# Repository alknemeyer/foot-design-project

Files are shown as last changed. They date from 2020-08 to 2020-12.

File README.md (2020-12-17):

# Foot Design Project

_Code for the hopper being used to test foot designs_

This project was developed by [Alexander Knemeyer](https://github.com/alknemeyer) on a laptop running PopOS (_basically_ Ubuntu). I can't think of a reason why the project wouldn't work under Windows/MacOS, though the commands were all written with Linux in mind. Please don't hesitate to ask me questions!

Read the following four blog posts to get you up and running with Python workflows and embedded dev:
* Communicating with embedded systems using Python, [part 1](https://alknemeyer.github.io/embedded-comms-with-python/) and [part 2](https://alknemeyer.github.io/embedded-comms-with-python-part-2/)
* [A workflow for remote development](https://alknemeyer.github.io/remote-notebooks/)
* [Improving the jupyter notebook workflow](https://alknemeyer.github.io/jupyter-notebook-workflow/)

The last two are themed on "remote" and "jupyter notebook" development, but are useful for this project

## The robot

A rough model of the robot, describing angle conventions, lengths, etc. Made using https://editor.method.ac/ - a free online svg editor. Stick to this! And keep it up to date!

<p align="center">

</p>

### Equipment used

| Item | Name |
| --- | --- |
| Motor controller | [ODrive](https://odriverobotics.com/) |
| Motor x2 | [T-motor U-10 80rpm/V](http://store-en.tmotor.com/goods.php?id=362) |
| Motor encoder x2 | [HEDL-5640-A13](https://www.mouser.co.za/ProductDetail/Broadcom-Avago/HEDL-5640A13?qs=RuhU64sK2%252Bv3nPu5sOD%2FhQ==) |
| Force sensor | [OptoForce OMD-45-FH-2000N](http://schlu.com/pdf/Optoforce_Sensore_di_forza_3D_OMD-45-FH-2000N_1.5_EN.pdf) |
| Sensor logger | [Parts list](https://github.com/African-Robotics-Unit/sensor-logger)|

### Wiring things together

The general setup is:
| | | Connection type |
|-|-|---:|
| laptop | sensor logger | USB cable |
| laptop | ODrive | USB cable |
| ODrive | motor encoders | Premade connectors. See below |
| ODrive | motors | Three thick wires for each motor |
| ODrive "AUX" port | 10 Ohm shunt resistor | Short thick wires |
| laptop | OptoForce | USB connection |

I can't remember how to do the calculation for the required resistance/power, unfortunately!

The motor encoders have pins as follows:

| pin | type | | pin | type |
|-----|---|-|-----|---|
| 1 | NC | | 2 | +5V  |
| 3 | GND | | 4 | NC |
| 5 | not(A) | | 6 | A |
| 7 | not(B) | | 8 | B |
| 9 | not(I) | | 10  | I |

where NC = No Connection, and I = Index = Z

When looking at the connector, they correspond to the diagram below, where crosses over numbers indicates pins which aren't connected:

<p align="center">
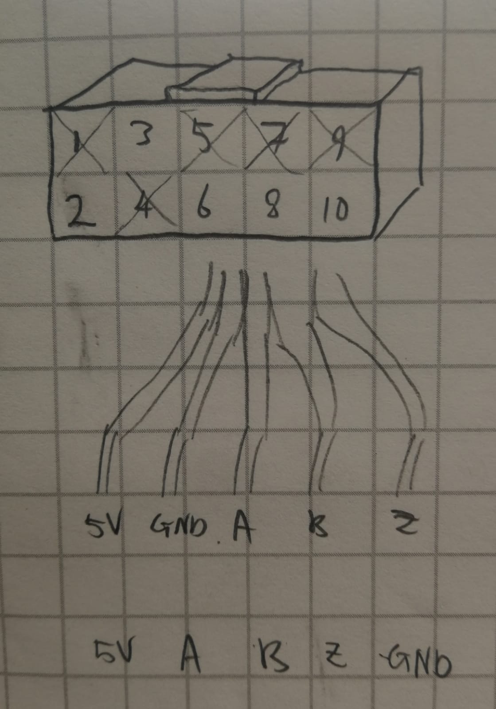
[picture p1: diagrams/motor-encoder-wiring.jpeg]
motor encoder wiring diagram

</p>

Now, the connection works as follows:

<p align="center">
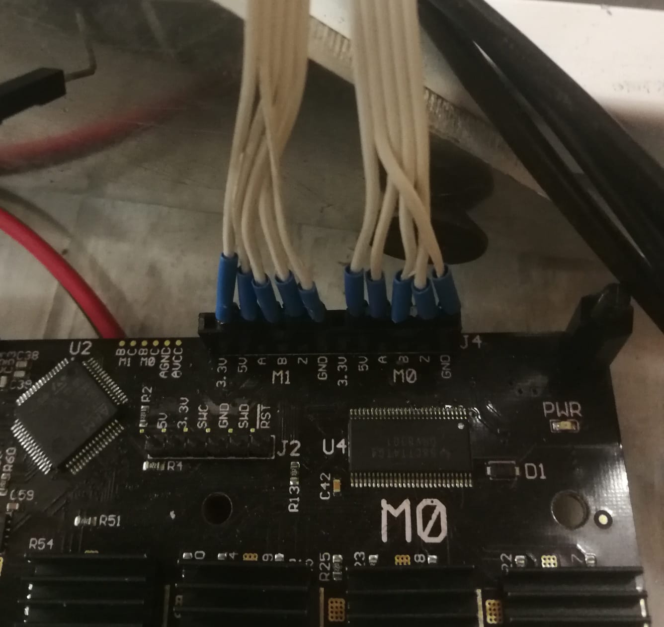
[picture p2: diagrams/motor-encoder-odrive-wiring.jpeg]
photo of connection between motor encoder and ODrive

</p>

Note that the second line from the left (ground, as shown by the hand-drawn diagram) crosses over the lines and ends up at the ground pin of the ODrive. When looking at the robot from the front, the left motor is motor 0 (M0)

There seemed to be noise on the encoder index lines, causing the encoders to "reset" randomly. Capacitors were added (not shown in the diagram) but the index lines are still not working properly

## Software environment setup

### Download this repo
Clone this repo, and make sure to download the submodules too:

    $ git clone --recurse-submodules https://github.com/alknemeyer/foot-design-project

One of the modules is [typesieve](https://github.com/alknemeyer/typesieve) - it contains a bunch of type annotations, which make it easier to work on ODrive code without having it plugged in. Please read the project's README!

### Python
Install conda or miniconda, then either install dependancies manually:

```bash
# create a virtual environment named "foot-design" using
# conda, and activate it
$ conda create --name foot-design
$ conda activate foot-design

# install the main dependancies
$ conda install jupyterlab matplotlib serial sympy

# some dependancies aren't available via conda
# install those via pip:
$ conda install pip
$ python -m pip install --upgrade https://github.com/alknemeyer/optoforce/tarball/main

# IF you want to do trajectory optimisation,
# install the following:
$ python -m pip install odrive physical-education==0.1.2 pyomo
$ conda install -c conda-forge cyipopt  # get ipopt the easy way

# there might be more install instructions for your
# particular OS: https://docs.odriverobotics.com/
# eg. on ubuntu, I have to install "udev rules"

# after you've done that, plug in the ODrive, power it
# externally (ie >=24V from a bench power supply) and
# then enter:
$ odrivetool

# on my laptop, a few lines of errors get displayed saying
# "[stuff] was never awaited", but after ~10 seconds you
# should see something like:
# "Connected to ODrive 20603595524B as odrv0"
# in cyan text. If so -- great! You're connected to the odrive
```

OR start from a conda `environment.yml` file, which will install the exact same versions of dependancies under a virtual environment named `foot-design`:

    $ conda env create --file=environment.yml

If you want to create an environment file to document eg. new or updated dependancies, run

    $ conda env export > environment.yml

If using vs code, you'll need to update the `""python.pythonPath"` setting in `.vscode/settings.json` to your actual virtual environment, or click on a notification if it pops up

### ODrive
You have a choice now - you can keep the software + firmware versions that are being used at the time of writing (ODrive Python library + firmware version 0.4.12) or upgrade to a new version. My feeling is that it's better to use the latest version since that's what the docs reflect, what people on forums will most readily help with, and _probably_ most bug-free. See the instructions on the ODrive website

Tip: if using Ubuntu, you might need to run `odrivetool dfu` with `sudo`! You'll know if you get a bug about `ValueError: The device has no langid`

Moving on: you'll also need to configure and calibrate the motors. Plug them in before running the code in `scripts/config_motors.py`. Do so by either copy-pasting the code into the `odrivetool` REPL, or by just running:

    $ python scripts/config_motors.py

The values in the script come from the from T-motor link above.

N.B: the script should be re-run if you change the power supply! For example, from bench power supply (for testing) to 10kW supply

### Sensor logger
It's probably a good idea to re-flash the sensor logger firmware before you use it (just in case someone else has messed with it). However, if the same firmware is still uploaded, it should just work as is. It can be imported an used as a module (eg. see `controller.py`) or run as main to just log to a file:

    $ python sensor_logger/scripts/receive_comms.py

It should also make a plot of the data

## Control
~~This is where will start to go wrong.~~ I'm sure you'll do great!

First off, read Chris's excellent documentation in the `RAM - Robotic Test Leg` folder, bearing in mind that the documentation was written a ago, and that it's not up to date

Now, there are three ongoing approaches to controlling the leg:

### 1. ODrive's PID control
The "current working" control method is documented in [controller.py](./controller.py), [scripts/lib.py](./scripts/lib.py) and [scripts/test.py](./scripts/test.py). It basically uses the ODrive's built in PID position control and some geometry to place the foot by controlling leg and positions

### 2. Impedance control on motor angles
A "sort of working" approach is a super simple PD current-controller on the motor angles. We get control loop times of around 1.5ms (bearing in mind this is Python, and it'll depend on the speed of your laptop).

<p align="center">
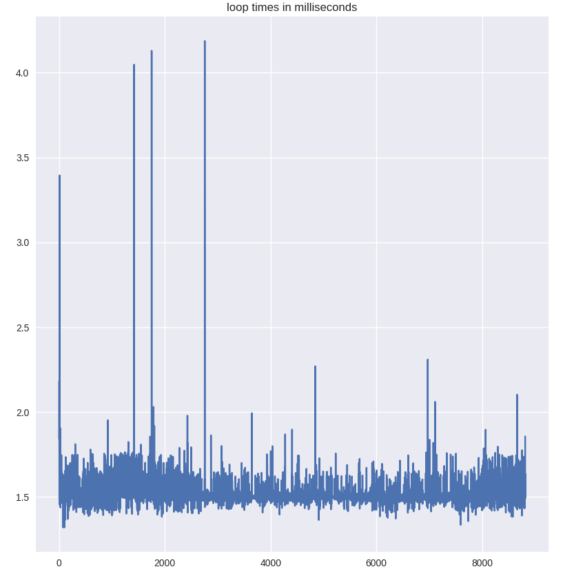
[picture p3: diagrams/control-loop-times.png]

</p>

Anecdotally, the controller is unstable if the control loop time is extended to 10/15 ms via `time.sleep(...)` statements.

If that time is dominated by ODrive stuff (eg blocking comms), then there isn't much we can do. Otherwise, if it's from the Python side, we can experiment with using a different python implementation (like pypy). But no use it in stressing about it until it becomes a problem!

See [`impedance_controller.py`](./impedance_controller.py) for the implementation

### 3. Impedance control of foot position
Last is the "not working but possibly close" controller. The idea is that we define the foot in polar coordinates, and try to make it behave as if it were a spring-damper system with parameters we can set. See [`scripts/impedance-control.ipynb`](./scripts/impedance-control.ipynb) for the derivation and [`impedance_controller.py`](./impedance_controller.py) for the buggy implementation.

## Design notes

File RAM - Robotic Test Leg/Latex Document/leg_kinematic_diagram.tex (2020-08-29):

\documentclass{standalone}
\usepackage{tikz}
\usetikzlibrary{quotes,angles,arrows}
\begin{document}
\begin{tikzpicture}[scale=0.5]
	\draw[thick,->] (0,0) -- (15,0) node[anchor=north west] {x} coordinate (x);
	\draw[thick,->] (0,0) -- (0,31) node[anchor=south east] {y} coordinate (y);
	
	\draw[-*] (0,0) coordinate (o)
	-- node[below] {$l_1$} (13.067,4.279) coordinate (b)
	-- node[right] {$l_2$} (4.154,27.635) coordinate (c);
	
	\draw[-*] (0,0) coordinate (d)
	-- node[below] {$l_1$} (-11.232,7.931) coordinate (e)
	-- node[left] {$l_2$} (4.154,27.635) node[left] {$(x'_e, y'_e)$}
	-- node[left] {$l_3$} (6,30) coordinate (g) node[right] {$(x_e, y_e)$};
	\draw[dashed, red] (0,0) -- node[right] {$r$} (6,30);
	\draw[dashed, red] (0,0) -- node[left] {$r'$} (4.154,27.635);
	
	\draw pic["$\lambda$",draw,<->,angle eccentricity=1.1,angle radius=2cm] {angle=c--o--e};
	\draw pic["$\theta_1$",draw,<->,angle eccentricity=1.2,angle radius=1cm] {angle=x--o--e};
	\draw pic["$\theta_2$",draw,<->,angle eccentricity=1.2,angle radius=2cm] {angle=x--o--b};
	\draw[red] pic["$\phi$",draw,<->,angle eccentricity=1.1,angle radius=4cm] {angle=x--o--g};
	\draw[red] pic["$\phi'$",draw,<->,angle eccentricity=1.1,angle radius=3cm] {angle=x--o--c};
\end{tikzpicture}
\end{document}

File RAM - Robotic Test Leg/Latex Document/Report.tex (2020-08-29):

\documentclass[11pt, titlepage]{article}

\usepackage{wasysym}
\usepackage{caption}
\usepackage{amsmath}
\usepackage[subpreambles]{standalone}
\usepackage{graphicx}
\graphicspath{ {./images/} }

\usepackage{hyperref}
\hypersetup{
	colorlinks=true,     
    urlcolor=blue,
    linkcolor=black
}

\usepackage{geometry}
\geometry{margin=1in}

\begin{document}
\title{RAM Robotic Test Leg}
\author{by Christopher Mailer (MLRCHR001)}
\maketitle

\tableofcontents

\newpage
\section{Design Calculations}
\subsection{Specifications}
\begin{itemize}
	\item T-Motor U10 Plus 80KV
	\item Coaxial 5 bar linkage leg design
	\item Place to attach foot designs
	\item Components purchased from RS Components
	\item Use of 2:1 timing belt for lightweight quasi-direct-drive actuation
\end{itemize}

\subsection{T-Motor U10 Plus 80KV}
\begin{table}[h]
\centering
\caption*{Motor Properties}
\begin{tabular}{ l l }
\hline
 Pole Pairs & 21 \\
 Weight & $405\,g$ \\
 Internal Resistance & $135\,m\Omega$ \\
 Startup Torque & 7.5\,Nm \\
 Max Rated Speed & $4000\,rpm$ \\
 Max Continuous Current & $25\,A$ \\
 Max Continuous Power & $1200\,W$ \\\hline
\end{tabular}
\end{table}

\subsection{Timing Belt Selection}
\subsubsection{Profile and Pitch}
The 'T' timing belt profile was chosen as it is a standard profile providing the largest selection of belts and pulleys on RS Components.\newline
The selected timing belt pitch type of T5 was minimum pitch which would support transmission of the 1.2\,kW of power produced by each of the motors while still providing a large selection of belt sizes on RS Components. Additional considerations were that a larger pitch such as the T10 pitch would be accompanied by a larger belt width, thus increasing the overall size of the design. A smaller pitch such as the T2.5 on the other hand would be challenging to accurately 3D print the pulley tooth profile.

\subsubsection{Material}
The predominant T5 timing belt type on RS Components was the polyurethane CONTI SYNCROFLEX with steel tension members. Polyurethane belts have better abrasion resistance than rubber belts.

\newpage
\subsection{Small Pulley Sizing}
Based on the dimensions of the motor and pulley mounting interface, the smallest pulley pitch diameter which can be mounted to the motor while still accommodating the mounting bolts is $\diameter 36$.

\begin{equation}
	z_1 = \frac{d_1\cdot \pi}{t} = \frac{(36)(\pi)}{5} = 22.62\,teeth
\end{equation}

The next available standard number of pulley teeth  is 24 resulting in the following tooth pitch

\begin{equation}
	d_1 = \frac{z\cdot t}{\pi} = \frac{(24)(5)}{\pi} = 38.20\,mm	
\end{equation}

The centre to centre distance of the small and large pulleys is currently unknown but could be estimated to be approximately 90\,mm, thus allowing the number of engaged teeth on the small pulley to be estimated

\begin{equation}
	z_e = z_1 (0.5-\frac{d_2-d_1}{2\pi C}) = (24)(0.5-\frac{(2)(38.20)-38.20}{(2)(\pi)(90)}) \approx11
\end{equation}

\subsection{Timing Belt Width}
The small pulley is the limiting component in the calculating of the timing belt width as it is where maximum tooth shear is experienced.

\begin{table}[!h]
\centering
\caption*{Belt Specific Tooth Strength at 4000\,rpm from datasheet}
\begin{tabular}{ l r r r l}\hline
		Specific Torque & $M_{spec}$ & = & 1.91 & Ncm/cm \\
		Specific Power & $P_{spec}$ & = & 3.81 & W/cm \\\hline
\end{tabular}
\end{table}

\begin{table}[!h]
\centering
\caption*{Given conditions}
\begin{tabular}{ l r r r l}\hline
	Power & $P$ & = & 1.2 & kW \\
	Torque & $M$ & = & 7.5 & Nm \\
	Number of Teeth & $z_1$ & = & 24 & Nm \\
	Teeth in Mesh & $z_e$ & = & 11 & teeth \\\hline
\end{tabular}
\end{table}

\subsubsection{Tooth Shear Strength}
Calculation of the belt width based on power
\begin{equation}
	b = \frac{10^4\cdot P}{z_1 \cdot z_e \cdot P_{spec}} = \frac{(10^4)(1.2)}{(24)(11)(3.81)} = 11.93\,mm
\end{equation}
Calculation of the belt width based on torque
\begin{equation}
	b = \frac{10^3\cdot M}{z_1 \cdot z_e \cdot M_{spec}} = \frac{(10^3)(7.5)}{(24)(11)(1.91)} = 14.87\,mm
\end{equation}
The next standard belt width which exceeds both of these is 16\,mm

\subsubsection{Tension Member Strength}
The maximum allowable tension for a T5 16\,mm wide timing belt is 570\,N
\begin{equation}
	F_u = \frac{2 \cdot 10^3 \cdot M}{d_1} = \frac{(2)(10^3)(7.5)}{38.20} = 393\, N < 570\,N
\end{equation}
Therefore the selected timing belt will be able to withstand the loads

\subsection{Timing Belt Length}
The centre to centre distance of the timing belt needs to be larger than 90\,mm to provide sufficient clearance between the pulleys, but should also be kept to a minimum to ensure a compact design.

\begin{table}[!h]
\centering
\caption*{Given conditions}
\begin{tabular}{ l r r r l}\hline
	Centre to centre distance & $C$ & $\ge$ & 90 & mm \\
	Small pulley no. of teeth & $z_1$ & = & 24 & teeth \\
	Large pulley no. of teeth & $z_2$ & = & 48 & teeth \\\hline
\end{tabular}
\end{table}

\begin{equation}
	d_i = \frac{z_i\cdot p}{\pi}
\end{equation}

\begin{equation}
	\theta_1 = 2\cdot\arccos(\frac{d_2-d_1}{2\cdot C}) = 2,71\,rad
\end{equation}

\begin{equation}
	\theta_2 = 2\pi -\theta_1 = 3,57\,rad
\end{equation}

\begin{equation}
	L = 2\cdot C\cdot \sin(\frac{\theta_1}{2}) + \theta_1\cdot\frac{d_1}{2} + \theta_2\cdot\frac{d_2}{2} = 364,07\,mm
\end{equation}

The next available standard timing belt length is 365\,mm which requires a centre to centre distance of 90,48\,mm.

\subsection{Selected Timing Belt}
CONTI SYNCROFLEX T5 Timing Belt, 73 teeth, 365\,mm length, 16\,mm width

\newpage
\subsection{Shaft Loading Condition}
The maximum forces experienced by each of the shafts will be during landing when the legs are fully extended and the force will be transmitted directly to the shafts and not shared by the motors as torque.

\subsubsection{Leg Impact Force}
Approximating the rubber pad on the base of the foot as a spring and assuming all of the gravitational potential energy is transferred to spring energy, the following can be determined:

\begin{equation}
	E_p = mgh
\end{equation}

\begin{equation}
	E_s = \frac{1}{2}k\delta^2
\end{equation}

\begin{equation}
	\delta = \sqrt{\frac{2E_p}{k}}
\end{equation}

The rubber pad on the base of the foot was approximated to have a spring constant of $30\times10^3\,N/m$. The test rails also only allow for a maximum jump height of 1\,m. The maximum ground reaction force experienced by the leg during landing is therefore;

\begin{equation}
	F_{max} = \sqrt{2mghk} = \sqrt{(2)(3)(9.81)(1)(30\times10^3)} = 1329\,N
\end{equation}

This is a conservative estimate as other means of energy dissipation are ignored. This force will be evenly distributed between each leg linkage producing 665\,N on the end of each shaft.

\subsubsection{Belt Tension}
Assuming belt tensioned to full capacity of $P_1 = 570\,N$
\begin{equation}
	P_2 = P_1-\frac{2M}{d_1} = 570 - \frac{(2)(7.5)}{0.0382} = 141.4\,N
\end{equation}

The centre to centre distance of timing belt pulleys, and therefore angle of wrap of the belts at this stage in the design is unknown. Instead the belts are conservatively assumed to be parallel, resulting in all of the tension being transmitted to the shaft.

\begin{equation}
	P_{res} = P_1 + P_2 = 711.4
\end{equation}

\subsubsection{Combined Load}
The legs will exert maximum force on the shaft during landing when in the fully contracted or extended states. In this case the impact force from the legs will be transmitted to the shaft almost directly upwards. The angle of the belt tensions is acting at $45^{\circ}$ to the vertical. The shaft is also expected to transmit 15\,Nm of torque after the 2:1 speed reduction from the motor.
\begin{table}[h!]
\centering
	\begin{tabular}{c c c}
		$P_{x}$ & = & 503\,N \\
		$P_{y}$ & = & 503\,N \\
		$M$ & = & 15\,Nm \\
	\end{tabular}
\end{table}

\newpage
\subsection{Inner Shaft BMD}
\noindent\textbf{Side View}
\begin{figure}[h]
\centering
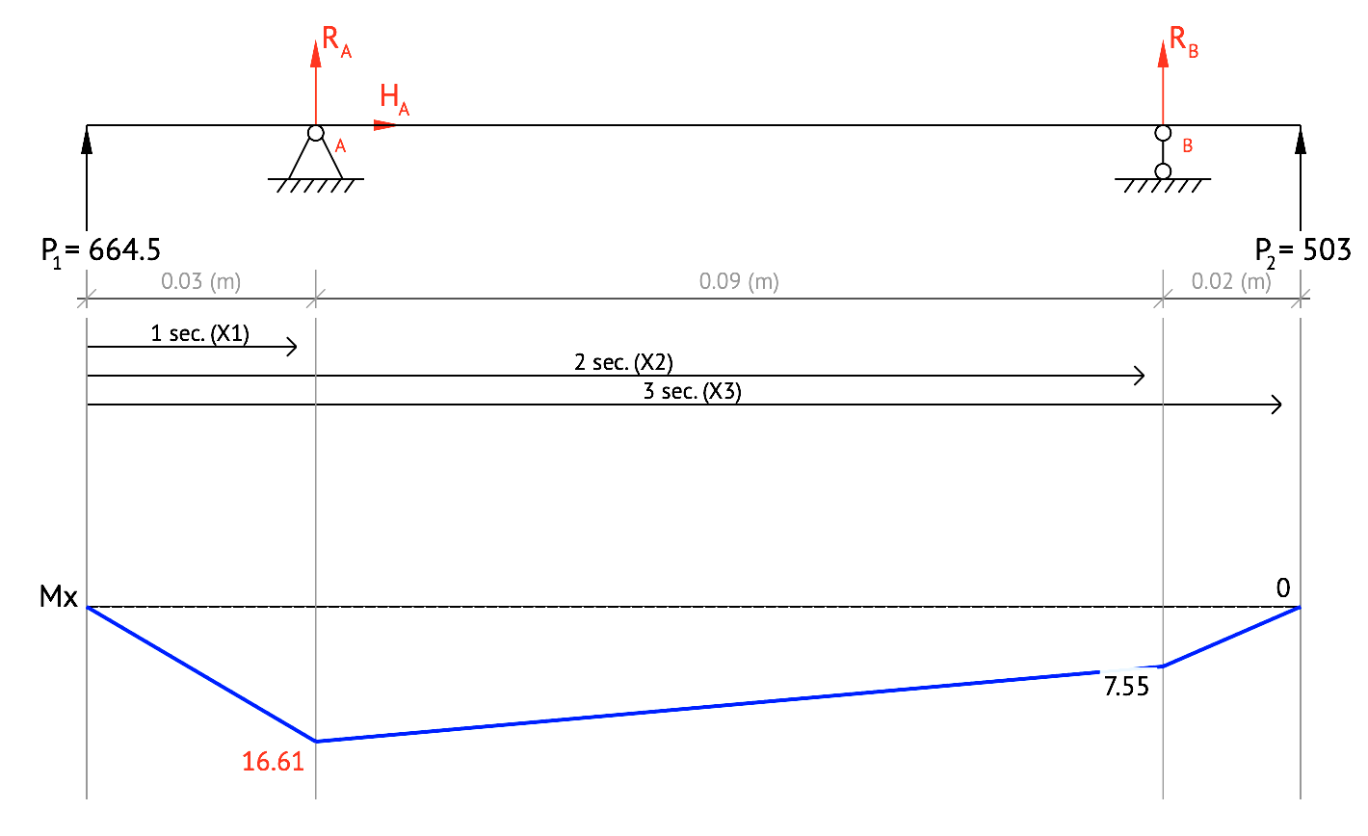
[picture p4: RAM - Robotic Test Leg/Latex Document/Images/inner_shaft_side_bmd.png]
	
	\caption{Inner shaft side view bending moment diagram \href{beamguru.com/online/beam-calculator/?save=e3c807530bc8028842f255e179b1241b}{BeamGuru}}
\end{figure}

${R_{A}}_y = -762.53\,N$ \hfill
${R_{B}}_y = -404.97\,N$\hfill
$M_{xz}=16.61$\newline

\noindent\textbf{Top View}
\begin{figure}[h]
\centering
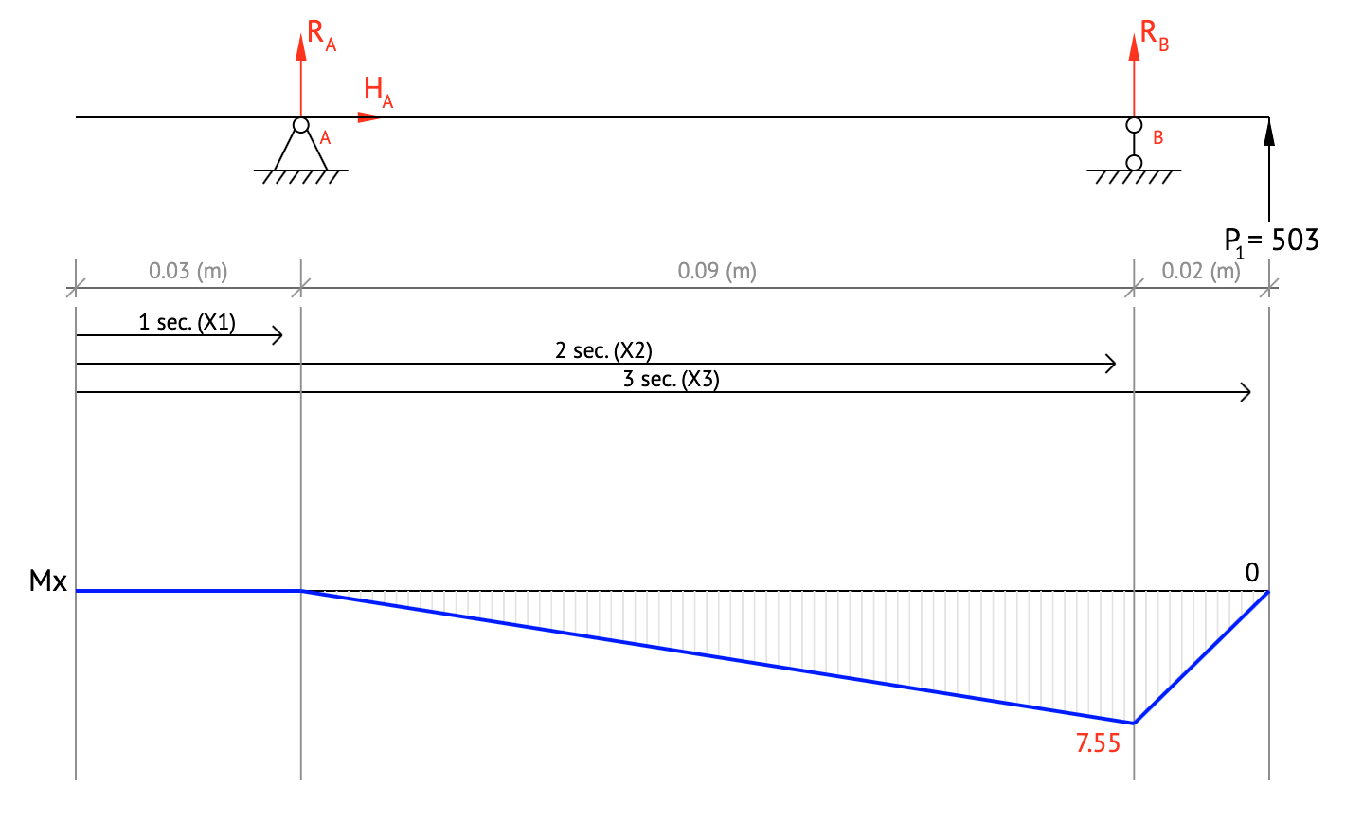
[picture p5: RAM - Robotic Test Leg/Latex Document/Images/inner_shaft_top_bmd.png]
	
	\caption{Inner shaft top view bending moment diagram \href{beamguru.com/online/beam-calculator/?save=88759fc0e73600b1a941d8defae4d6b8}{BeamGuru}}
\end{figure}

${R_{A}}_x = 81.57\,N$ \hfill
${R_{B}}_x = -584.57\,N$\hfill
$M_{yz}=0$\newline

\noindent\textbf{Resultant}\newline
Critical section at leftmost bearing
$$M = \sqrt{{M_{xz}}^2 + {M_{yz}}^2} = 16.61\,Nm$$
$$T = 15\,Nm$$

\newpage
\subsection{Outer Shaft BMD}
\noindent\textbf{Side View}
\begin{figure}[h]
\centering
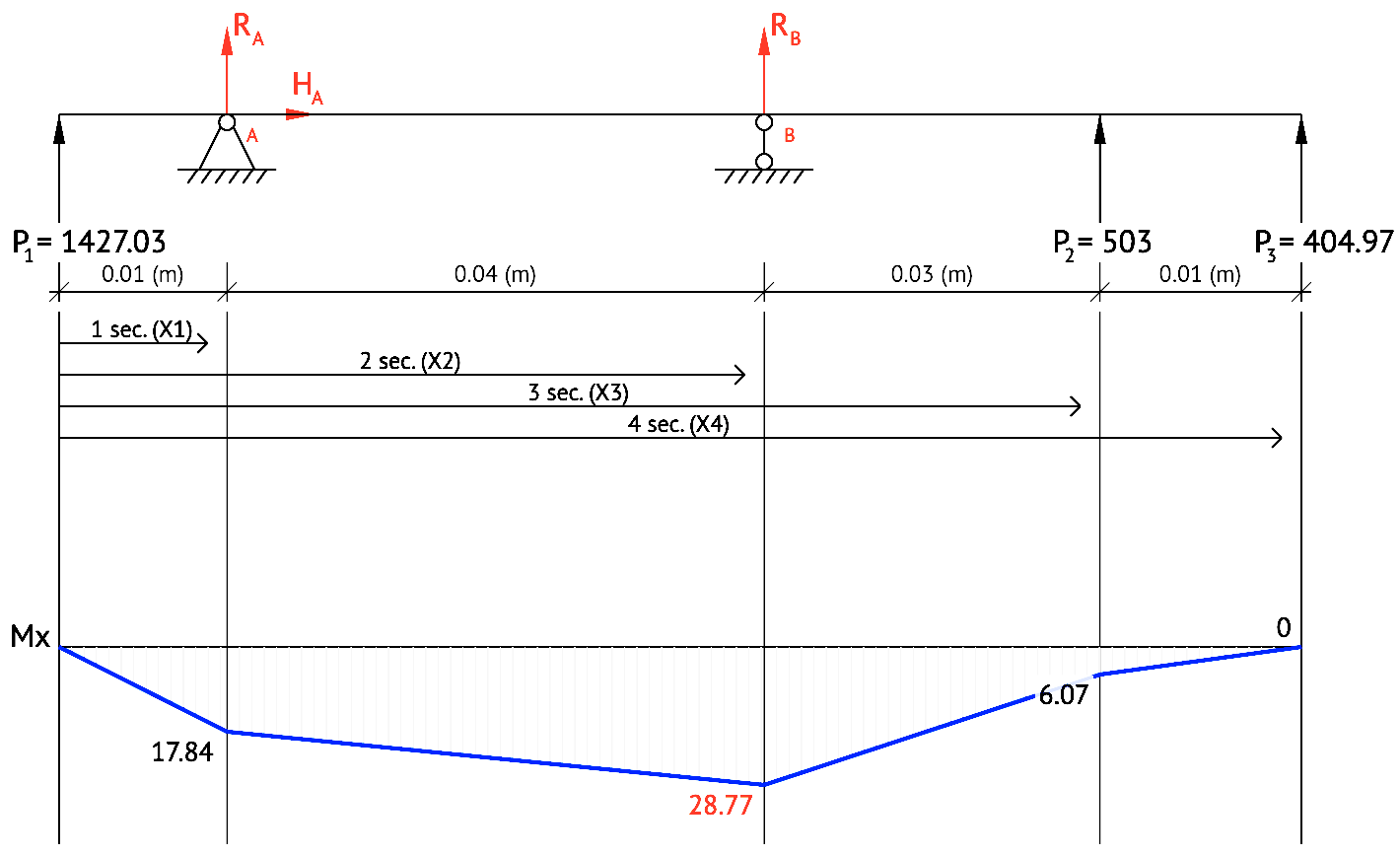
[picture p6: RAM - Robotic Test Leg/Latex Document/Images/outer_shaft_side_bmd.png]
	
	\caption{Outer shaft side view bending moment diagram \href{beamguru.com/online/beam-calculator/?save=e3c807530bc8028842f255e179b1241b}{BeamGuru}}
\end{figure}

${R_{A}}_y = -1153.63\,N$ \hfill
${R_{B}}_y = -1181.37\,N$\hfill
$M_{xz}=28.77$\newline

\noindent\textbf{Top View}
\begin{figure}[h]
\centering
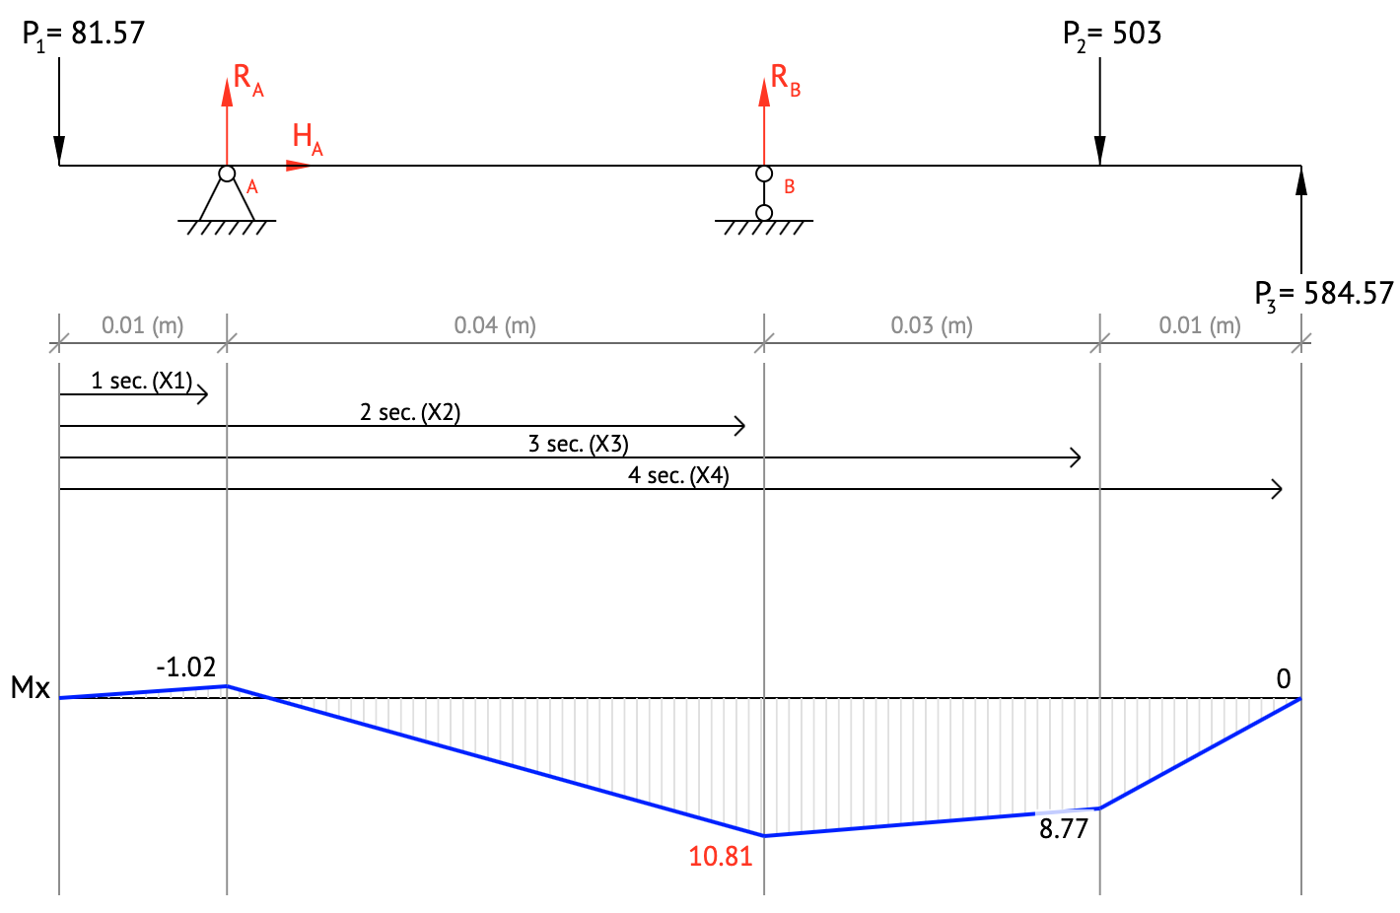
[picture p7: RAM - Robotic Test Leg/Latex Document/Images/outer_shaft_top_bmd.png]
	
	\caption{Outer shaft top view bending moment diagram \href{beamguru.com/online/beam-calculator/?save=88759fc0e73600b1a941d8defae4d6b8}{BeamGuru}}
\end{figure}

${R_{A}}_x = 377.26\,N$ \hfill
${R_{B}}_x = -377.26\,N$\hfill
$M_{yz}=-1.02$\newline

\noindent\textbf{Resultant}\newline
Critical section at rightmost bearing
$$M = \sqrt{{M_{xz}}^2 + {M_{yz}}^2} = 30.73\,Nm$$
$$T = 15\,Nm$$

\subsection{Shaft Sizing}
\begin{equation}
	\sigma = \frac{Mr}{I} = \frac{32M}{\pi{d_o}^3(1-\frac{d_i}{d_0}^4)}
\end{equation}
\begin{equation}
	\tau = \frac{Tr}{J} = \frac{16 T}{\pi{d_o}^3(1-\frac{d_i}{d_0}^4)}
\end{equation}

\subsubsection{Material}
The shaft will be made from 304 Stainless Steel, as this was available in the workshop, thus the Maximum Distortion Energy Theory will be a sufficient failure theory.\newline\newline
$S_u = 215\,MPa$
\begin{equation}
	{\sigma_b}^2 + 3\tau^2 \le (\frac{S_u}{RF})^2
\end{equation}
The following calculations were done in the spreadhseet \textit{Shaft and Belt Calculations}

\subsubsection{Inner Shaft Size}
The Inner Shaft diameter selection was an iterative process driven by the Outer Shaft diameters and the available bearings on RS Components. A diameter of $\diameter12\,mm$ was selected as this provided a reserve factor of 1.7 and ensured a reasonable selection of roller bearings. A larger inner shaft would have resulted in a significantly larger outer shaft, greatly increasing the weight of the design.

$$D_o = 12\,mm$$
$$RF = 1,7$$

\subsubsection{Outer Shaft Size}
The outer diameter of the shaft was selected to be $\diameter20\,mm$ based on bearing availability on RS Components. With the goal of keeping size and mass to a minimum, the smallest roller bearings were selected which required the Outer Shaft to have an inner diameter of $\diameter16\,mm$. This produced a reserve factor of 3. To create a shoulder for the bearings, the remaining portion of the shaft has an inner diameter of $\diameter14\,mm$.

$$D_o = 20\,mm$$
$$D_i = 16\,mm$$
$$RF=3,0$$

\newpage
\section{Manufacture}
\subsection{3D Printing}

The following parts are 3D printed

\begin{table}[h]
\centering
\begin{tabular}{ l c}
	\textbf{Part Name} & \textbf{Qty} \\\hline
	Inner Timing Belt Gear & 1 \\
	Outer Timing Belt Gear & 1 \\
	Motor Mounting & 2 \\
	Support Brace & 1 \\
	Encoder Shaft & 2 \\
	Leg Spacer & 3 \\\hline
\end{tabular}	
\end{table}

\subsubsection{Printer Settings}
The Cura Ender 3 presets were used with the following modifications.

\begin{table}[h]
\centering
	\begin{tabular}{r l}
	\hline
		Printer & Ender 3 Pro\\
		Material & PLA \\
		Printing Temp. & $200^{\circ}$ \\
		Printing Speed & 50\,mm/s \\
		Layer Height & 0.2\,mm \\
		Infill Density & 60\% \\
		Infill Pattern & Cubic \\
		Adhesion Type & Raft \\
		\hline
	\end{tabular}
\end{table}

\subsubsection{Considerations}
The main challenge with 3D printed parts was shrinkage. To compensate holes were printed 4\% larger and reamed afterwards to remove seams. The shrinkage also resulted in the timing belt initially not being properly tensioned. New output pulleys were printed with 1\,mm larger outer diameters which corrected the problem.

\subsubsection{Additional Machining}
\begin{itemize}
	\item Holes need to be drilled out to remove seams
\end{itemize}

\newpage
\subsection{Laser Cutting}
The following parts are laser cut

\begin{table}[h]
\centering
\begin{tabular}{ l c c c}
	\textbf{Part Name} & \textbf{Material} & \textbf{Thickness} & \textbf{Qty} \\\hline
	Mounting Plate & 5182 Aluminium & 3\,mm & 1 \\
	Inner Short Leg Link & 5083 Aluminium & 10\,mm & 1\\
	Outer Short Leg Link & 5083 Aluminium & 10\,mm & 1 \\
	Extra Long Leg Link & 5083 Aluminium & 10\,mm & 1 \\
	Long Leg Link & 5083 Aluminium & 10\,mm & 1 \\
	\hline
\end{tabular}	
\end{table}

\subsubsection{Considerations}
Laser cutting thick material produces a rough edge and the cut does not remain perpendicular to the material surface. Thus, holes should be undersized before laser cutting and then later reamed to the correct size on a drill press to ensure a smooth finish and perpendicularity.

\subsubsection{Additional Machining}
\begin{itemize}
	\item The Mounting Plate requires sanding to remove rough edges
	\item The leg links require the bearing seats to be machined. This is a counterbore to a depth of 5\,mm. A cutting tool on a drill press achieves this.
	\item The holes for the shoulder bolts need to be drilled and tapped for the M5 shoulder bolt
	\item The holes for the inner and outer output shafts need to be reamed to the correct sizes
\end{itemize}

\newpage
\subsection{Machining}
The following parts were machined by the UCT workshop

\begin{table}[h]
\centering
\begin{tabular}{ l c c}
	\textbf{Part Name} & \textbf{Material} & \textbf{Qty} \\\hline
	Flange & 6082 Aluminium & 1 \\
	Motor Shaft (Short) & 6082 Aluminium & 1 \\
	Motor Shaft (Long) & 6082 Aluminium & 1 \\
	Inner Shaft & 304 Stainless Steel & 1 \\
	Outer Shaft & 304 Stainless Steel & 1 \\
	Timing Belt Pulley 24T & NA & 2 \\\hline
\end{tabular}	
\end{table}

\subsubsection{Considerations}
The machining of the Timing Belt Pulleys 24T is simple and can be done with a drill press to reduce time and cost.

\subsubsection{Additional Machining}
\begin{itemize}
	\item All of the shafts are slightly oversized for the bearings. They therefore need to be carefully sanded down until a locational fit with the inner race is achieved.
\end{itemize}

\newpage
\section{Future Modifications}
\subsection{Gear Ratio}
Very little analysis was done on the optimum gear ratio for the leg. If it is later found that a different gear ratio is required, then the following parameters will need to be changed to implement this.

\begin{enumerate}
	\item The new inner and outer shaft pulley number of teeth and outer diameter will need to be modified to produce the required reduction ratio. These pulleys will in turn need to be 3D printed again.
	\item A new centre to centre distance between the motors and output shafts will need to be calculated based on the new pulley diameters and the available timing belt lengths.
	\item The mounting plate SolidWorks file will need to be updated with the new centre to centre distance and laser cut. 
\end{enumerate}

\subsection{Leg Dimensions}
Baleka's legs were used as a basis for the proportions of the leg links, however very little analysis was done on the optimum lengths. As future design changes to the legs is inevitable, the SolidWorks part dimensions were laid out to in such a way to make changes to the pivot to pivot lengths simple to modify.

\newpage
\section{Leg Kinematics}
\begin{figure}[h]
	\centering
	\includestandalone[width=12cm]{leg_kinematic_diagram}
	\caption{Kinematic diagram of leg}
\end{figure}

The red dashed lines represent "virtual legs" in the polar coordinate space. This representation makes computing leg compliance significantly simpler.\newline\newline
\begin{equation}
Let\ \lambda = \frac{\theta_1 - \theta_2}{2}
\end{equation}

\newpage
\subsection{Forward Kinematics (Excluding $l_3$)}
\subsubsection{Cartesian Coordinates}
\begin{equation}
	x'_e = \left(l_1\cos\left(\frac{\theta_1-\theta_2}{2}\right)+\sqrt{{l_2}^2-{l_1}^2\sin^2\left(\frac{\theta_1-\theta_2}{2}\right)}\right)\cos\left(\frac{\theta_1+\theta_2}{2}\right)
\end{equation}
\begin{equation}
	y'_e = \left(l_1\cos\left(\frac{\theta_1-\theta_2}{2}\right)+\sqrt{{l_2}^2-{l_1}^2\sin^2\left(\frac{\theta_1-\theta_2}{2}\right)}\right)\sin\left(\frac{\theta_1+\theta_2}{2}\right)
\end{equation}\newline

For computing the Jacobian

\begin{equation}
\resizebox{.9 \textwidth}{!} 
{
$\frac{\partial x'_e}{\partial \theta_1} = \cos\left(\frac{\theta_1+\theta_2}{2}\right)\left(-\frac{1}{2}l_1\sin(\lambda)-\frac{{l_1}^2\sin(\lambda)\cos(\lambda)}{2\sqrt{{l_2}^2-{l_1}^2\sin^2(\lambda)}}\right)
- \frac{1}{2}\sin\left(\frac{\theta_1+\theta_2}{2}\right)\left(l_1\cos(\lambda)+\sqrt{{l_2}^2-{l_1}^2\sin^2(\lambda)}\right)$
}
\end{equation}
\begin{equation}
\resizebox{.9 \textwidth}{!} 
{
$\frac{\partial x'_e}{\partial \theta_2} = \cos\left(\frac{\theta_1+\theta_2}{2}\right)\left(\frac{1}{2}l_1\sin(\lambda)+\frac{{l_1}^2\sin(\lambda)\cos(\lambda)}{2\sqrt{{l_2}^2-{l_1}^2\sin^2(\lambda)}}\right)
- \frac{1}{2}\sin\left(\frac{\theta_1+\theta_2}{2}\right)\left(l_1\cos(\lambda)+\sqrt{{l_2}^2-{l_1}^2\sin^2(\lambda)}\right)$
}
\end{equation}
\begin{equation}
\resizebox{.9 \textwidth}{!} 
{
$\frac{\partial y'_e}{\partial \theta_1} = \sin\left(\frac{\theta_1+\theta_2}{2}\right)\left(-\frac{1}{2}l_1\sin(\lambda)-\frac{{l_1}^2\sin(\lambda)\cos(\lambda)}{2\sqrt{{l_2}^2-{l_1}^2\sin^2(\lambda)}}\right)
+ \frac{1}{2}\cos\left(\frac{\theta_1+\theta_2}{2}\right)\left(l_1\cos(\lambda)+\sqrt{{l_2}^2-{l_1}^2\sin^2(\lambda)}\right)$
}
\end{equation}
\begin{equation}
\resizebox{.9 \textwidth}{!} 
{
$\frac{\partial y'_e}{\partial \theta_2} = \sin\left(\frac{\theta_1+\theta_2}{2}\right)\left(\frac{1}{2}l_1\sin(\lambda)+\frac{{l_1}^2\sin(\lambda)\cos(\lambda)}{2\sqrt{{l_2}^2-{l_1}^2\sin^2(\lambda)}}\right)
+ \frac{1}{2}\cos\left(\frac{\theta_1+\theta_2}{2}\right)\left(l_1\cos(\lambda)+\sqrt{{l_2}^2-{l_1}^2\sin^2(\lambda)}\right)$
}
\end{equation}

$$
	\textbf{J} = 
\begin{bmatrix}
\frac{\partial x'_e}{\partial \theta_1} &&
\frac{\partial x'_e}{\partial \theta_2} \\
\frac{\partial y'_e}{\partial \theta_1} &&
\frac{\partial y'_e}{\partial \theta_2}
\end{bmatrix}
$$

\subsubsection{Polar Coordinates}
\begin{equation}
	\phi' = \frac{\theta_1 + \theta_2}{2}
\end{equation}
\begin{equation}
	r' = l_1\cos(\frac{\theta_1 - \theta_2}{2})+\sqrt{{l_2}^2-{l_1}^2\sin^2(\frac{\theta_1 - \theta_2}{2})}
\end{equation}

For computing the Jacobian

\begin{equation}
	\frac{\partial \phi'_e}{\partial \theta_1} = \frac{\partial \phi'_e}{\partial \theta_2} = \frac{1}{2}
\end{equation}

\begin{equation}
	\frac{\partial r'_e}{\partial \theta_1} = {-\frac{1}{2}l_1\sin(\lambda)-\frac{{l_1}^2\sin(\lambda)\cos(\lambda)}{2\sqrt{{l_2}^2-{l_1}^2\sin^2(\lambda)}}}
\end{equation}

\begin{equation}
	\frac{\partial r'_e}{\partial \theta_2} = {\frac{1}{2}l_1\sin(\lambda)+\frac{{l_1}^2\sin(\lambda)\cos(\lambda)}{2\sqrt{{l_2}^2-{l_1}^2\sin^2(\lambda)}}}
\end{equation}

$$
	\textbf{J} = 
\begin{bmatrix}
\frac{\partial \phi'_e}{\partial \theta_1} &&
\frac{\partial \phi'_e}{\partial \theta_2} \\
\frac{\partial r'_e}{\partial \theta_1} &&
\frac{\partial r'_e}{\partial \theta_2}
\end{bmatrix}
$$

\newpage
\subsection{Forward Kinematics (Including $l_3$)}
\subsubsection{Cartesian Coordinates}
\begin{equation}
\resizebox{.9 \textwidth}{!} 
{
$x_e = \left(l_1\cos\left(\frac{\theta_1-\theta_2}{2}\right)+\sqrt{{l_2}^2-{l_1}^2\sin^2\left(\frac{\theta_1-\theta_2}{2}\right)}\right)\cos\left(\frac{\theta_1+\theta_2}{2}\right) + l_3\cos(\arcsin(\frac{l_1\sin(\frac{\theta_1-\theta_2}{2})}{l_2}))$
}
\end{equation}

\begin{equation}
\resizebox{.9 \textwidth}{!} 
{
$y_e = \left(l_1\cos\left(\frac{\theta_1-\theta_2}{2}\right)+\sqrt{{l_2}^2-{l_1}^2\sin^2\left(\frac{\theta_1-\theta_2}{2}\right)}\right)\sin\left(\frac{\theta_1+\theta_2}{2}\right) + \frac{l_3l_1\sin(\frac{\theta_1-\theta_2}{2})}{l_2}$
}
\end{equation}\newline

For computing the Jacobian

\begin{equation}
\resizebox{.9 \textwidth}{!} 
{
$\frac{\partial x_e}{\partial \theta_1} = \cos\left(\frac{\theta_1+\theta_2}{2}\right)\left(-\frac{1}{2}l_1\sin(\lambda)-\frac{{l_1}^2\sin(\lambda)\cos(\lambda)}{2\sqrt{{l_2}^2-{l_1}^2\sin^2(\lambda)}}\right)
- \frac{1}{2}\sin\left(\frac{\theta_1+\theta_2}{2}\right)\left(l_1\cos(\lambda)+\sqrt{{l_2}^2-{l_1}^2\sin^2(\lambda)}\right)
- \frac{{l_1}^2l_3\sin(\lambda)\cos(\lambda)}{2{l_2}^2\sqrt{1-\frac{{l_1}^2\sin^2(\lambda)}{{l_2}^2}}}$
}
\end{equation}

\begin{equation}
\resizebox{.9 \textwidth}{!} 
{
$\frac{\partial x_e}{\partial \theta_2} = \cos\left(\frac{\theta_1+\theta_2}{2}\right)\left(\frac{1}{2}l_1\sin(\lambda)+\frac{{l_1}^2\sin(\lambda)\cos(\lambda)}{2\sqrt{{l_2}^2-{l_1}^2\sin^2(\lambda)}}\right)
- \frac{1}{2}\sin\left(\frac{\theta_1+\theta_2}{2}\right)\left(l_1\cos(\lambda)+\sqrt{{l_2}^2-{l_1}^2\sin^2(\lambda)}\right)
+ \frac{{l_1}^2l_3\sin(\lambda)\cos(\lambda)}{2{l_2}^2\sqrt{1-\frac{{l_1}^2\sin^2(\lambda)}{{l_2}^2}}}$
}
\end{equation}

\begin{equation}
\resizebox{.9 \textwidth}{!} 
{
$\frac{\partial y_e}{\partial \theta_1} = \sin\left(\frac{\theta_1+\theta_2}{2}\right)\left(-\frac{1}{2}l_1\sin(\lambda)-\frac{{l_1}^2\sin(\lambda)\cos(\lambda)}{2\sqrt{{l_2}^2-{l_1}^2\sin^2(\lambda)}}\right)
+ \frac{1}{2}\cos\left(\frac{\theta_1+\theta_2}{2}\right)\left(l_1\cos(\lambda)+\sqrt{{l_2}^2-{l_1}^2\sin^2(\lambda)}\right)
+ \frac{l_3l_1\cos(\lambda)}{2l_2}$
}
\end{equation}

\begin{equation}
\resizebox{.9 \textwidth}{!} 
{
$\frac{\partial y_e}{\partial \theta_2} = \sin\left(\frac{\theta_1+\theta_2}{2}\right)\left(\frac{1}{2}l_1\sin(\lambda)+\frac{{l_1}^2\sin(\lambda)\cos(\lambda)}{2\sqrt{{l_2}^2-{l_1}^2\sin^2(\lambda)}}\right)
+ \frac{1}{2}\cos\left(\frac{\theta_1+\theta_2}{2}\right)\left(l_1\cos(\lambda)+\sqrt{{l_2}^2-{l_1}^2\sin^2(\lambda)}\right)
- \frac{l_3l_1\cos(\lambda)}{2l_2}$
}
\end{equation}

$$
	\textbf{J} = 
\begin{bmatrix}
\frac{\partial x_e}{\partial \theta_1} &&
\frac{\partial x_e}{\partial \theta_2} \\
\frac{\partial y_e}{\partial \theta_1} &&
\frac{\partial y_e}{\partial \theta_2}
\end{bmatrix}
$$

\newpage
\section{ODrive}
\subsection{Notes}
\begin{itemize}
	\item It is significantly easier to use a python script to edit the settings on the ODrive than using the ODrive Tool shell. A lot of time was initially wasted navigating through heavily nested settings in the shell.
\end{itemize}

\subsection{Configuration}
The file \textit{configuration.py} will setup the ODrive to control the T-Motor U10 Plus 80KV with feedback from the E6B2-CWZ6C Encoder. The script saves the settings to memory on the ODrive, so it only needs to be run once at the beginning.

\end{document}

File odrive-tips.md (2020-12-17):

# ODrive "knowledge"
This doc summarizes tips for using the ODrive which can be found in the official documentation, but have been useful for this project, so have been copied here for discoverability

### Tuning
See the [tuning guide](https://docs.odriverobotics.com/control.html#Tuning). The process used for this robot is as follows:

Copy-paste the folloing code into the `odrivetool` REPL, line by line:

```python
# set ax to odrv0.axis0 or axis1. Each motor *should* require
# the same gains
ax = odrv0.axis0
# ax = odrv0.axis1

ax.requested_state = AXIS_STATE_FULL_CALIBRATION_SEQUENCE
# wait...
ax.requested_state = AXIS_STATE_CLOSED_LOOP_CONTROL
# use ax.requested_state = AXIS_STATE_IDLE to stop vibrating etc

# defaults
ax.controller.config.pos_gain = 20.0 # [(counts/s) / counts]
ax.controller.config.vel_gain = 5.0 / 10000.0 # [A/(counts/s)]
ax.controller.config.vel_integrator_gain = 10.0 / 10000.0 # [A/((counts/s) * s)]

ax.controller.config.vel_integrator_gain = 0

# increase vel_gain until it's unstable, then request idle state
ax.controller.config.vel_gain = 8.0 / 10000.0   # vibrates at 16.0

# increase pos_gain until it's unstable, then bring back to smoothness
ax.controller.config.pos_gain = 80.0     # should be 120.0

# integrator gain
def set_int_gain(bandwidth_hz):
    vel_gain = ax.controller.config.vel_gain
    ax.controller.config.vel_integrator_gain = 0.5 * bandwidth_hz * vel_gain

set_int_gain(10)

odrv0.save_configuration()
odrv0.reboot()
```

### Live plotting
It may be useful to live plot the setpoint vs motor output. Do so using,
```python
start_liveplotter(lambda:[odrv0.axis0.encoder.pos_estimate,
                          odrv0.axis0.controller.pos_setpoint,
                          odrv0.axis1.encoder.pos_estimate,
                          odrv0.axis1.controller.pos_setpoint])
```
You don't need to run that in a new terminal or anything - it runs in the background. Press enter if you don't see the `In [x] :` prompt

### Tip for debugging:
From the [ODrive troubleshooting](https://docs.odriverobotics.com/troubleshooting) page:

```python
# show errors
>>> dump_errors(odrv0)

# show errors and then clear em. This is useful if an
# error occurs, you fix it, and then need to manually
# clear error flags before the ODrive works again
>>> dump_errors(odrv0, True)
```

### Optional nicer print for `odrv0.reboot()`:
When the odrive reboots, it raises an error in your Python code. Do this too often and you'll stop noticing real errors. A better approach is to do the following, which specifically catches the error thrown by a reboot:

```python
from fibre.protocol import ChannelBrokenException
try:
    odrv0.reboot()
except ChannelBrokenException:
    print('Lost connection because of reboot')
```

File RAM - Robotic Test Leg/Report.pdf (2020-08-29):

## RAM Robotic Test Leg

by Christopher Mailer (MLRCHR001)

January 10, 2020

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
5 ODrive | 16

## 1 Design Calculations

### 1.1 Specifications

- T-Motor U10 Plus 80KV
- Coaxial 5 bar linkage leg design
- Place to attach foot designs
- Components purchased from RS Components
- Use of 2:1 timing belt for lightweight quasi-direct-drive actuation

### 1.2 T-Motor U10 Plus 80KV

Motor Properties

Pole Pairs | 21
Weight | 405 g
Internal Resistance | 135 mΩ
Startup Torque | 7.5 Nm
Max Rated Speed | 4000 rpm
Max Continuous Current 25 A Max Continuous Power 1200 W

### 1.3 Timing Belt Selection

### 1.3.1 Profile and Pitch

The ’T’ timing belt profile was chosen as it is a standard profile providing the largest selection of belts and pulleys on RS Components.
The selected timing belt pitch type of T5 was minimum pitch which would support transmission of the 1.2 kW of power produced by each of the motors while still providing a large selection of belt sizes on RS Components. Additional considerations were that a larger pitch such as the T10 pitch would be accompanied by a larger belt width, thus increasing the overall size of the design. A smaller pitch such as the T2.5 on the other hand would be challenging to accurately 3D print the pulley tooth profile.

### 1.3.2 Material

The predominant T5 timing belt type on RS Components was the polyurethane CONTI SYN-CROFLEX with steel tension members. Polyurethane belts have better abrasion resistance than rubber belts.

### 1.4 Small Pulley Sizing

Based on the dimensions of the motor and pulley mounting interface, the smallest pulley pitch diameter which can be mounted to the motor while still accommodating the mounting bolts is !36.

z1 = d1 · π
t | = (36)(π)
5 | = 22.62 teeth | (1)

The next available standard number of pulley teeth is 24 resulting in the following tooth pitch

d1 = z · t
π = (24)(5)
π | = 38.20 mm | (2)

The centre to centre distance of the small and large pulleys is currently unknown but could be estimated to be approximately 90 mm, thus allowing the number of engaged teeth on the small pulley to be estimated

ze = z1(0.5 − d2 − d1

2πC ) = (24)(0.5 − ⁽²⁾⁽³⁸.20) − 38.20
(2)(π)(90) | ) ≈ 11 | (3)

### 1.5 Timing Belt Width

The small pulley is the limiting component in the calculating of the timing belt width as it is where maximum tooth shear is experienced.

Belt Specific Tooth Strength at 4000 rpm from datasheet

Specific Torque Mspec | = 1.91 Ncm/cm
Specific Power | Pspec | = 3.81 W/cm

Given conditions

Power | P = 1.2 kW
Torque | M = 7.5 Nm
Number of Teeth | z1 | = | 24 Nm
Teeth in Mesh | ze | = | 11 teeth

### 1.5.1 Tooth Shear Strength

Calculation of the belt width based on power

b = 10⁴ · P

z1 · ze · Pspec

= | (10⁴)(1.2)
(24)(11)(3.81) = 11.93 mm | (4)

Calculation of the belt width based on torque

b = 10³ · M

z1 · ze · Mspec

= | (10³)(7.5)
(24)(11)(1.91) = 14.87 mm | (5)

The next standard belt width which exceeds both of these is 16 mm

### 1.5.2 Tension Member Strength

The maximum allowable tension for a T5 16 mm wide timing belt is 570 N

Fu = 2 · 10³ · M
d1

= (2)(10³)(7.5)
38.20 | = 393 N < 570 N | (6)

Therefore the selected timing belt will be able to withstand the loads

### 1.6 Timing Belt Length

The centre to centre distance of the timing belt needs to be larger than 90 mm to provide sufficient clearance between the pulleys, but should also be kept to a minimum to ensure a compact design.

Given conditions

Centre to centre distance | C ≥ 90 mm
Small pulley no. of teeth | z1 | = 24 teeth
Large pulley no. of teeth | z2 | = 48 teeth

di = zi · p
π

(7)

θ1 = 2 · arccos(

d2 − d1
2 · C ) = 2, 71 rad | (8)
θ2 = 2π − θ1 = 3, 57 rad | (9)

L = 2 · C · sin(

θ1
2 ) + θ1 ·

d1
2 + θ2 ·

d2
2 = 364, 07 mm | (10)

The next available standard timing belt length is 365 mm which requires a centre to centre distance of 90,48 mm.

### 1.7 Selected Timing Belt

CONTI SYNCROFLEX T5 Timing Belt, 73 teeth, 365 mm length, 16 mm width

### 1.8 Shaft Loading Condition

The maximum forces experienced by each of the shafts will be during landing when the legs are fully extended and the force will be transmitted directly to the shafts and not shared by the motors as torque.

### 1.8.1 Leg Impact Force

Approximating the rubber pad on the base of the foot as a spring and assuming all of the gravita-tional potential energy is transferred to spring energy, the following can be determined:

Ep = mgh | (11)

Es = 1
2
kδ² | (12)

δ =

!2Ep
k | (13)

The rubber pad on the base of the foot was approximated to have a spring constant of 30 × 10³ N/m. The test rails also only allow for a maximum jump height of 1 m. The maximum ground reaction force experienced by the leg during landing is therefore;
Fmax = "2mghk = "(2)(3)(9.81)(1)(30 × 10³) = 1329 N | (14)

This is a conservative estimate as other means of energy dissipation are ignored. This force will be evenly distributed between each leg linkage producing 665 N on the end of each shaft.

### 1.8.2 Belt Tension

Assuming belt tensioned to full capacity of P1 = 570 N

P2 = P1 − ²M
d1

= 570 − ⁽²⁾⁽⁷.5)
0.0382 = 141.4 N | (15)

The centre to centre distance of timing belt pulleys, and therefore angle of wrap of the belts at this stage in the design is unknown. Instead the belts are conservatively assumed to be parallel, resulting in all of the tension being transmitted to the shaft.

Pres = P1 + P2 = 711.4 | (16)

### 1.8.3 Combined Load

The legs will exert maximum force on the shaft during landing when in the fully contracted or extended states. In this case the impact force from the legs will be transmitted to the shaft almost directly upwards. The angle of the belt tensions is acting at 45◦ to the vertical. The shaft is also expected to transmit 15 Nm of torque after the 2:1 speed reduction from the motor.

Px | = | 503 N
Py | = | 503 N
M = 15 Nm

### 1.9 Inner Shaft BMD

Side View

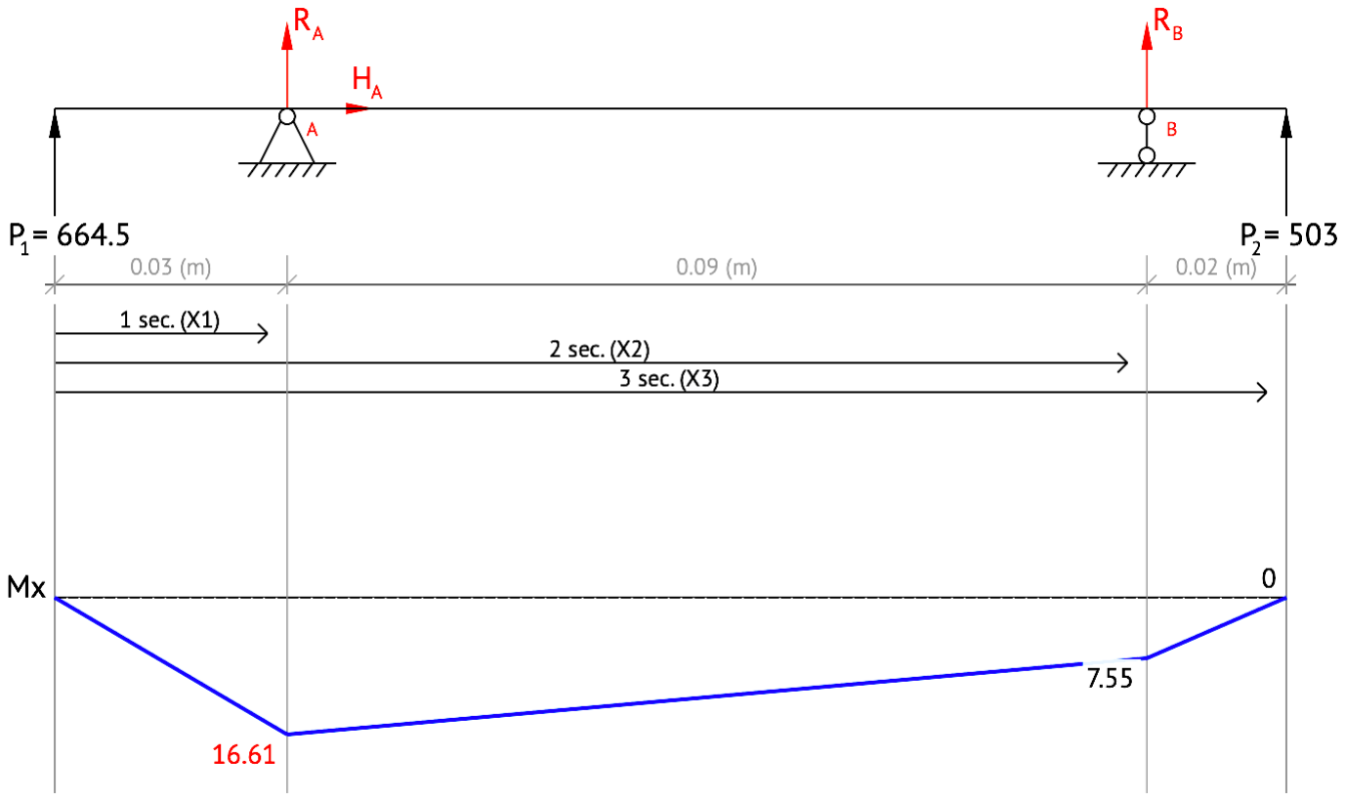
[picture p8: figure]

Figure 1: Inner shaft side view bending moment diagram BeamGuru

RAy = −762.53 N | RBy = −404.97 N | Mxz = 16.61

Top View

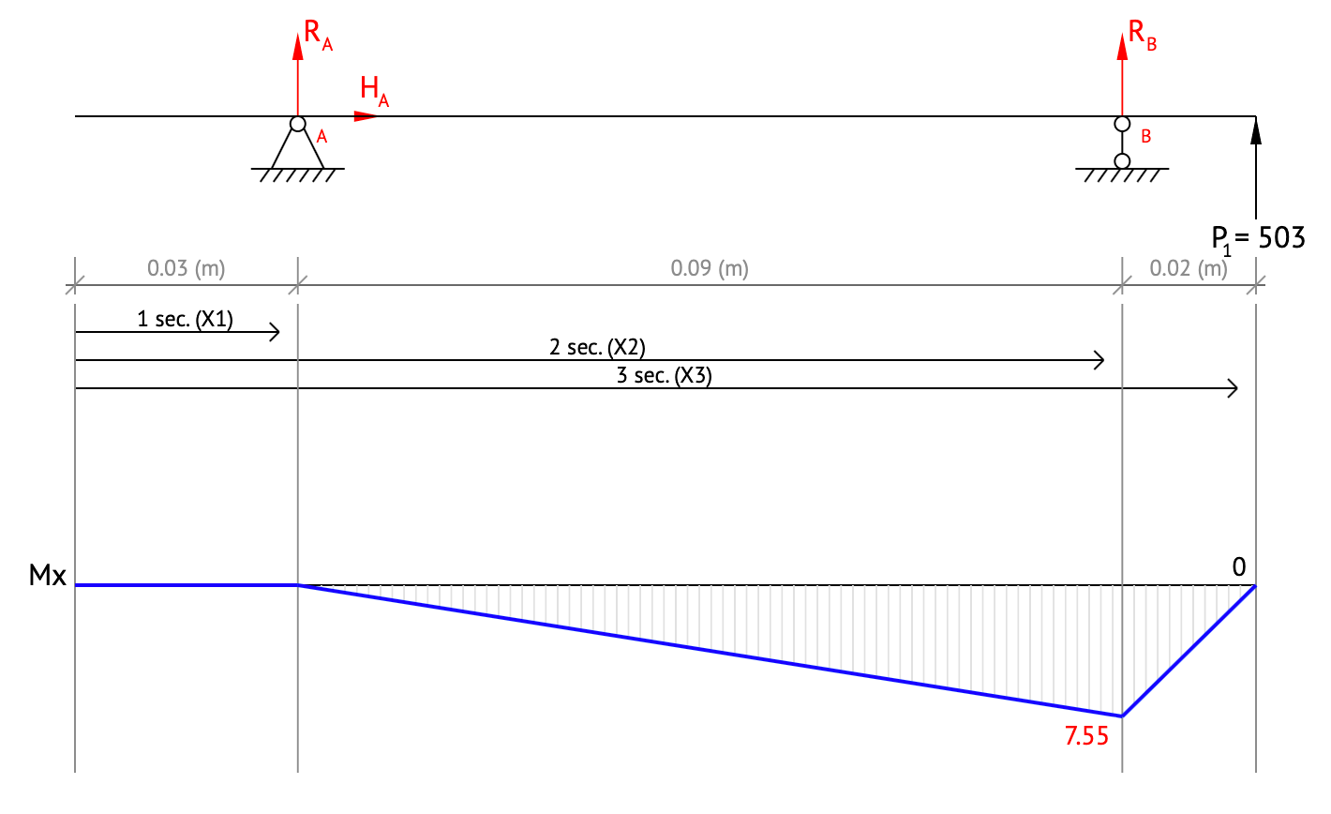
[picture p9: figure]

Figure 2: Inner shaft top view bending moment diagram BeamGuru

RAx = 81.57 N | RBx = −584.57 N | Myz = 0

Resultant
Critical section at leftmost bearing

M =

Mxz
| 2 + Myz 2 = 16.61 Nm
| T = 15 Nm

### 1.10 Outer Shaft BMD

Side View

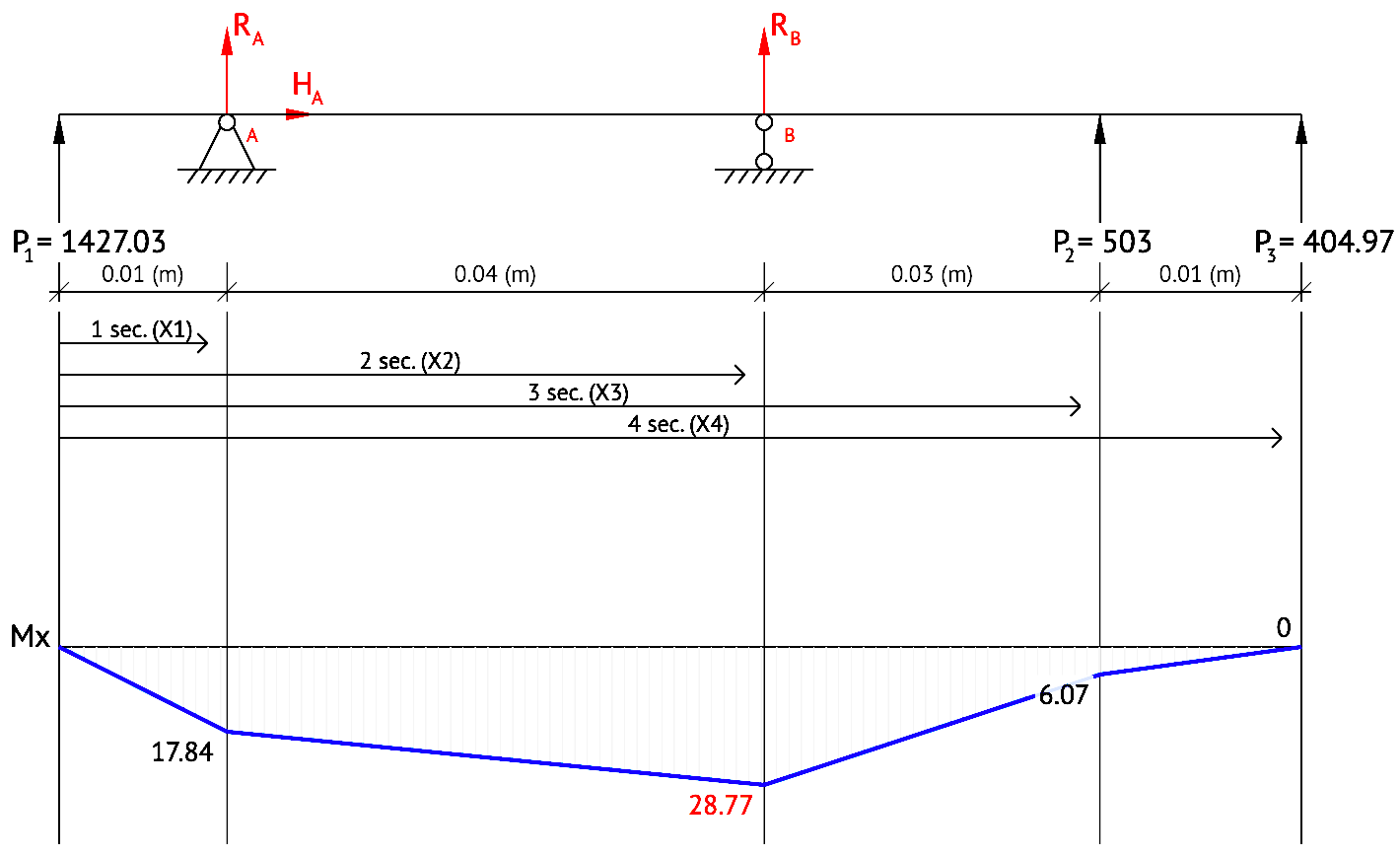
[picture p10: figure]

Figure 3: Outer shaft side view bending moment diagram BeamGuru

RAy = −1153.63 N | RBy = −1181.37 N | Mxz = 28.77

Top View

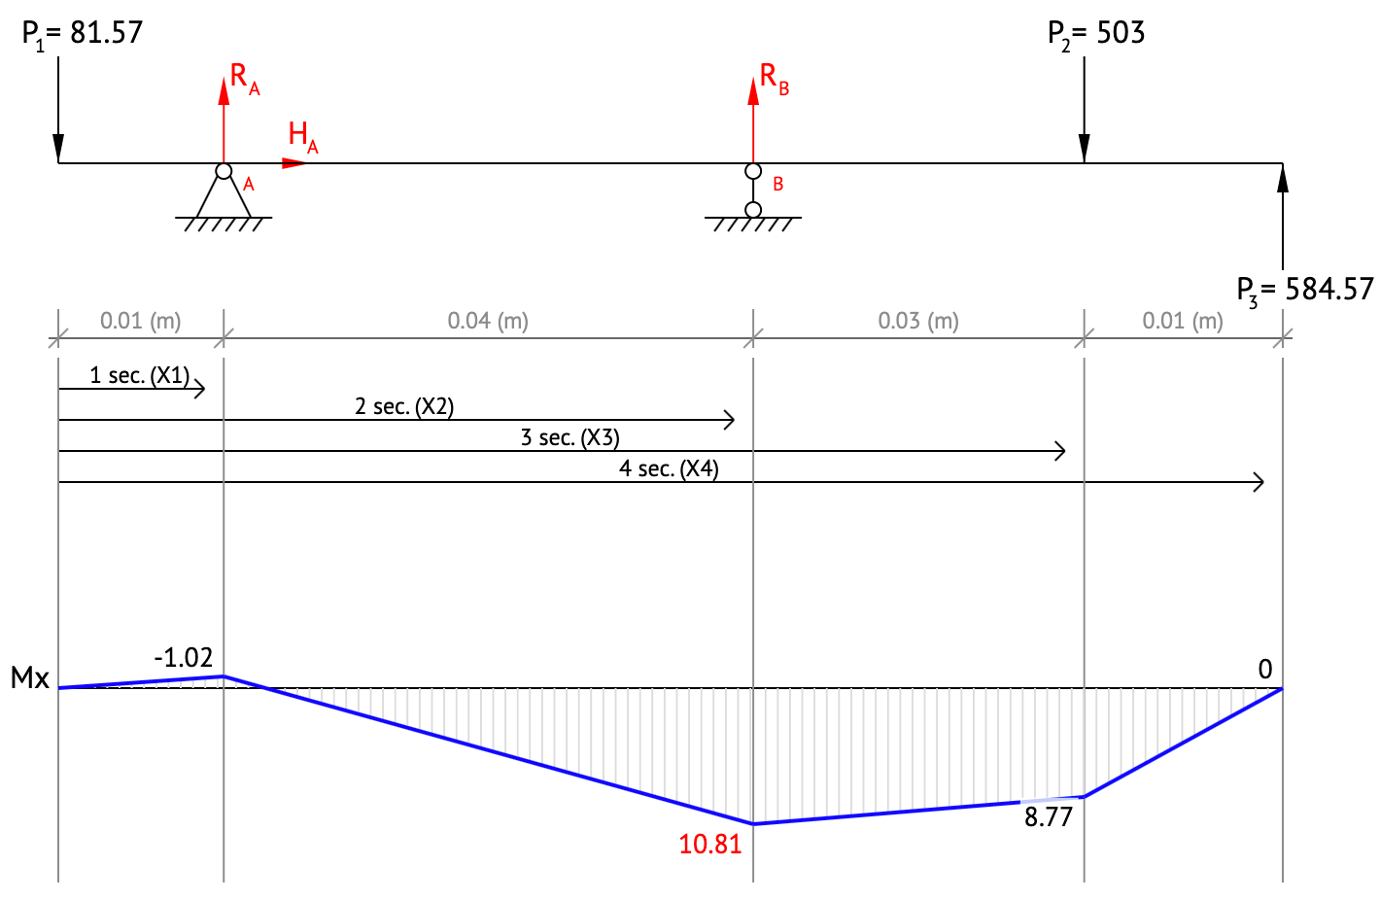
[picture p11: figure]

Figure 4: Outer shaft top view bending moment diagram BeamGuru

RAx = 377.26 N | RBx = −377.26 N | Myz = −1.02

Resultant
Critical section at rightmost bearing

M =

| Mxz 2 + Myz 2 = 30.73 Nm
| T = 15 Nm

### 1.11 Shaft Sizing

σ = Mr

I = 32M
πdo
| 3(1 − di
d0

4
)

(17)

τ = Tr

J = 16T
πdo
| 3(1 − di
d0

4
)

(18)

### 1.11.1 Material

The shaft will be made from 304 Stainless Steel, as this was available in the workshop, thus the Maximum Distortion Energy Theory will be a sufficient failure theory.

Su = 215 MPa
σb

2 + 3τ ² ≤ ( Su
RF )
2 | (19)

The following calculations were done in the spreadhseet Shaft and Belt Calculations

### 1.11.2 Inner Shaft Size

The Inner Shaft diameter selection was an iterative process driven by the Outer Shaft diameters and the available bearings on RS Components. A diameter of !12 mm was selected as this provided a reserve factor of 1.7 and ensured a reasonable selection of roller bearings. A larger inner shaft would have resulted in a significantly larger outer shaft, greatly increasing the weight of the design.

Do = 12 mm

RF = 1, 7

### 1.11.3 Outer Shaft Size

The outer diameter of the shaft was selected to be !20 mm based on bearing availability on RS Components. With the goal of keeping size and mass to a minimum, the smallest roller bearings were selected which required the Outer Shaft to have an inner diameter of !16 mm. This produced a reserve factor of 3. To create a shoulder for the bearings, the remaining portion of the shaft has an inner diameter of !14 mm.

Do = 20 mm

Di = 16 mm

RF = 3, 0

## 2 Manufacture

2.1 3D Printing

The following parts are 3D printed

Part Name | Qty
Inner Timing Belt Gear | 1
Outer Timing Belt Gear | 1
Motor Mounting | 2
Support Brace | 1
Encoder Shaft | 2
Leg Spacer | 3

### 2.1.1 Printer Settings

The Cura Ender 3 presets were used with the following modifications.

Printer Ender 3 Pro
Material PLA
Printing Temp. 200◦
Printing Speed 50 mm/s
Layer Height 0.2 mm
Infill Density 60%
Infill Pattern Cubic
Adhesion Type Raft

### 2.1.2 Considerations

The main challenge with 3D printed parts was shrinkage. To compensate holes were printed 4% larger and reamed afterwards to remove seams. The shrinkage also resulted in the timing belt initially not being properly tensioned. New output pulleys were printed with 1 mm larger outer diameters which corrected the problem.

### 2.1.3 Additional Machining

- Holes need to be drilled out to remove seams

### 2.2 Laser Cutting

The following parts are laser cut

Part Name | Material | Thickness Qty
Mounting Plate | 5182 Aluminium | 3 mm | 1
Inner Short Leg Link | 5083 Aluminium | 10 mm | 1
Outer Short Leg Link 5083 Aluminium | 10 mm | 1
Extra Long Leg Link | 5083 Aluminium | 10 mm | 1
Long Leg Link | 5083 Aluminium | 10 mm | 1

### 2.2.1 Considerations

Laser cutting thick material produces a rough edge and the cut does not remain perpendicular to the material surface. Thus, holes should be undersized before laser cutting and then later reamed to the correct size on a drill press to ensure a smooth finish and perpendicularity.

### 2.2.2 Additional Machining

- The Mounting Plate requires sanding to remove rough edges
- The leg links require the bearing seats to be machined. This is a counterbore to a depth of 5 mm. A cutting tool on a drill press achieves this.
- The holes for the shoulder bolts need to be drilled and tapped for the M5 shoulder bolt
- The holes for the inner and outer output shafts need to be reamed to the correct sizes

### 2.3 Machining

The following parts were machined by the UCT workshop

Part Name | Material | Qty
Flange | 6082 Aluminium | 1
Motor Shaft (Short) | 6082 Aluminium | 1
Motor Shaft (Long) | 6082 Aluminium | 1
Inner Shaft | 304 Stainless Steel | 1
Outer Shaft | 304 Stainless Steel | 1
Timing Belt Pulley 24T | NA | 2

### 2.3.1 Considerations

The machining of the Timing Belt Pulleys 24T is simple and can be done with a drill press to reduce time and cost.

### 2.3.2 Additional Machining

- All of the shafts are slightly oversized for the bearings. They therefore need to be carefully sanded down until a locational fit with the inner race is achieved.

## 3 Future Modifications

### 3.1 Gear Ratio

Very little analysis was done on the optimum gear ratio for the leg. If it is later found that a different gear ratio is required, then the following parameters will need to be changed to implement this.

1. The new inner and outer shaft pulley number of teeth and outer diameter will need to be modified to produce the required reduction ratio. These pulleys will in turn need to be 3D printed again.
2. A new centre to centre distance between the motors and output shafts will need to be calcu-lated based on the new pulley diameters and the available timing belt lengths.
3. The mounting plate SolidWorks file will need to be updated with the new centre to centre distance and laser cut.

### 3.2 Leg Dimensions

Baleka’s legs were used as a basis for the proportions of the leg links, however very little analysis was done on the optimum lengths. As future design changes to the legs is inevitable, the SolidWorks part dimensions were laid out to in such a way to make changes to the pivot to pivot lengths simple to modify.

## 4 Leg Kinematics

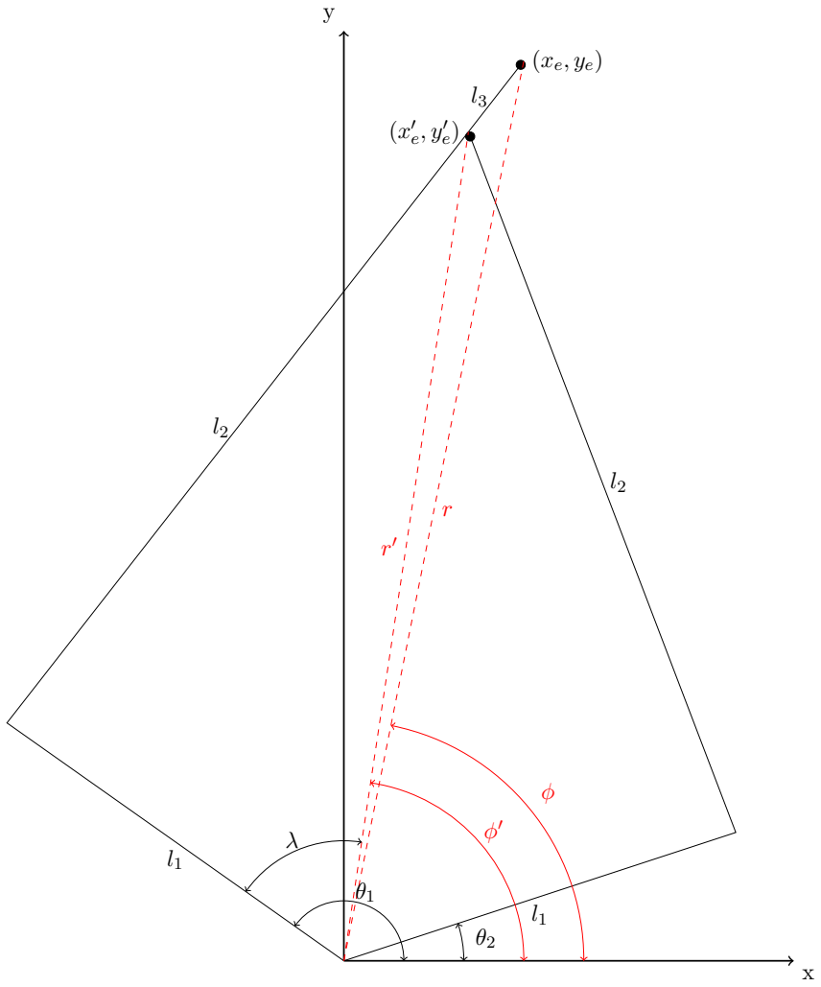
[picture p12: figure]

Figure 5: Kinematic diagram of leg

The red dashed lines represent ”virtual legs” in the polar coordinate space. This representation makes computing leg compliance significantly simpler.

Let λ = θ1 − θ2
2 | (20)

### 4.1 Forward Kinematics (Excluding l3)

### 4.1.1 Cartesian Coordinates

x′
e =

$
l1 cos

%θ1 − θ2

2

&
+

'

l2

2 − l1

2 sin²

%θ1 − θ2

2

&(
cos

%θ1 + θ2

2

&
(21)

y′
e =

$
l1 cos

%θ1 − θ2

2

&
+

'

l2

2 − l1

2 sin²

%θ1 − θ2

2

&(
sin

%θ1 + θ2

2

&
(22)

For computing the Jacobian

∂x′
e

∂θ1 = cos

)θ1+θ2

2

* %
−¹

2 l1 sin(λ) − l1

2 sin(λ) cos(λ)
2

√l2
2−l1

2 sin²(λ)

&
− ¹
2 sin

)θ1+θ2

2

* %
l1 cos(λ) +
l2

2 − l1

2 sin²(λ)

&
(23)

∂x′
e

∂θ2 = cos

)θ1+θ2

2

* %
1

2 l1 sin(λ) + l1

2 sin(λ) cos(λ)

2

√l2
2−l1

2 sin²(λ)

&
− ¹
2 sin

)θ1+θ2

2

* %
l1 cos(λ) +
l2

2 − l1

2 sin²(λ)

&
(24)

∂y′
e

∂θ1 = sin

)θ1+θ2

2

* %
−¹

2 l1 sin(λ) − l1

2 sin(λ) cos(λ)
2

√l2
2−l1

2 sin²(λ)

&
+ 1
2 cos

)θ1+θ2

2

* %
l1 cos(λ) +
l2

2 − l1

2 sin²(λ)

&
(25)

∂y′
e

∂θ2 = sin

)θ1+θ2

2

* %
1

2 l1 sin(λ) + l1

2 sin(λ) cos(λ)

2

√l2
2−l1

2 sin²(λ)

&
+ 1
2 cos

)θ1+θ2

2

* %
l1 cos(λ) +
l2

2 − l1

2 sin²(λ)

&
(26)

J =

+∂x′

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
### 4.1.2 Polar Coordinates

φ′ = θ1 + θ2
2 | (27)

r′ = l1 cos(

θ1 − θ2
2 ) +

!
l2

2 − l1

2 sin²(

θ1 − θ2
2 | ) | (28)

For computing the Jacobian

∂φ′
e
∂θ1

= ∂φ′
e
∂θ2

= 1
2 | (29)

∂r′
e
∂θ1

= −¹
2

l1 sin(λ) − l1

2 sin(λ) cos(λ)

2

l2

2 − l1

2 sin²(λ) | | (30)

∂r′
e
∂θ2

= 1
2

l1 sin(λ) +

l1

2 sin(λ) cos(λ)

2

l2

2 − l1

2 sin²(λ) | | (31)

J =

+∂φ′

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
### 4.2 Forward Kinematics (Including l3)

### 4.2.1 Cartesian Coordinates

xe =

%
l1 cos

)θ1−θ2

2

*
+

!
l2

2 − l1

2 sin²

)θ1−θ2

2

*&
cos

)θ1+θ2

2

*
+ l3 cos(arcsin(
l1 sin( θ1−θ2 2 | )
l2 | )) | (32)

ye =

%
l1 cos

)θ1−θ2

2

*
+

!
l2

2 − l1

2 sin²

)θ1−θ2

2

*&
sin

)θ1+θ2

2

*
+

l3l1 sin( θ1−θ2
2 | )
l2 | (33)

For computing the Jacobian

∂xe
∂θ1 = cos

)θ1+θ2

2

* %
−¹

2 l1 sin(λ) − l1

2 sin(λ) cos(λ)
2

√l2
2−l1

2 sin²(λ)

&
− ¹
2 sin

)θ1+θ2

2

* %
l1 cos(λ) +
l2

2 − l1

2 sin²(λ)

&
− l1

2l3 sin(λ) cos(λ)

2l2

2

!
1− l12 sin2(λ)
l22

(34)

∂xe
∂θ2 = cos

)θ1+θ2

2

* %
1

2 l1 sin(λ) + l1

2 sin(λ) cos(λ)
2

√l2
2−l1

2 sin²(λ)

&
− ¹
2 sin

)θ1+θ2

2

* %
l1 cos(λ) +
l2

2 − l1

2 sin²(λ)

&
+ l1

2l3 sin(λ) cos(λ)

2l2

2

!
1− l12 sin2(λ)
l22

(35)

∂ye
∂θ1 = sin

)θ1+θ2

2

* %
−¹

2 l1 sin(λ) − l1

2 sin(λ) cos(λ)
2

√l2
2−l1

2 sin²(λ)

&
+ 1
2 cos

)θ1+θ2

2

* %
l1 cos(λ) +
l2

2 − l1

2 sin²(λ)

&
+ l3l1 cos(λ)
2l2 (36)

∂ye
∂θ2 = sin

)θ1+θ2

2

* %
1

2 l1 sin(λ) + l1

2 sin(λ) cos(λ)
2

√l2
2−l1

2 sin²(λ)

&
+ 1
2 cos

)θ1+θ2

2

* %
l1 cos(λ) +
l2

2 − l1

2 sin²(λ)

&
− l3l1 cos(λ)
2l2 (37)

J =

+∂xe

∂θ1

∂xe
∂θ2 ∂ye

∂θ1

∂ye
∂θ2

,

## 5 ODrive

### 5.1 Notes

- It is significantly easier to use a python script to edit the settings on the ODrive than using the ODrive Tool shell. A lot of time was initially wasted navigating through heavily nested settings in the shell.

### 5.2 Configuration

The file configuration.py will setup the ODrive to control the T-Motor U10 Plus 80KV with feedback from the E6B2-CWZ6C Encoder. The script saves the settings to memory on the ODrive, so it only needs to be run once at the beginning.

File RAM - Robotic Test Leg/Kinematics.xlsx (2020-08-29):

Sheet: Including Toe
NB: Only edit highlighted cells
End Effector Position
x | 0 | mm
y | 300 | mm
Link Dimensions
L₁ | 137.5 | mm
L₂ | 250 | mm
L₃ | 30 | mm
r | 300.00 | mm
φ | 1.57 | rad | 90.0 | deg
x' | -13.69 | mm
y' | 273.30 | mm
r' | 273.65 | mm
φ' | 1.62 | rad | 92.9 | deg
λ | 1.14 | rad | 65.4 | deg
θ₁ | 2.76 | rad | 27.4 | deg
θ₂ | 0.48 | rad | 158.3 | deg
Plotting
 | x | y
Origin | 0.00 | 0.00 | mm
Joint 1 | -127.75 | 50.84 | mm
Joint 2 | 122.03 | 63.35 | mm
Joint 3 | -13.69 | 273.30 | mm
End Effector | 0.00 | 300.00 | mm
 | Polar Coordinates
 | J |  |  | Joint Speed |  |  |  | End Effector Speed
 |  |  | x | θ̇₁ | 0.00 | rad/s | = | φ̇ | #VALUE! | rad/s
 |  |  |  | θ̇₂ | 0.00 | rad/s |  | ṙ |  | mm/s
 | J⁻¹ |  |  | End Effector Speed |  |  |  | Joint Speed
 | #VALUE! |  | x | φ̇ | 0.0 | rad/s | = | θ̇₁ | #VALUE! | rad/s
 |  |  |  | ṙ | 0.0 | mm/s |  | θ̇₂ |  | rad/s
 | Jᵀ |  |  | End Effector Force |  |  |  | Joint Torque
 | 0.000 | 0.000 | x | Fᵩ | 0.0 | N | = | τ₁ | 0.0 | Nmm
 | 0.000 | 0.000 |  | Fᵣ | 0.0 | N |  | τ₂ | 0.0 | Nmm
 | (Jᵀ)⁻¹ |  |  | Joint Torque |  |  |  | End Effector Force
 | #NUM! |  | x | τ₁ | 0 | Nmm | = | Fᵩ | #NUM! | N
 |  |  |  | τ₂ | 0 | Nmm |  | Fᵣ |  | N
 | Cartesian Coordinates
 | J |  |  | Joint Speed |  |  |  | End Effector Speed
 | -134.680 | -138.624 | x | θ̇₁ | 6.00 | rad/s | = | ẋ | -1639.8 | mm/s
 | -82.353 | 68.665 |  | θ̇₂ | 6.00 | rad/s |  | ẏ | -82.1 | mm/s
 | J⁻¹ |  |  | End Effector Speed |  |  |  | Joint Speed
 | -0.003 | -0.007 | x | ẋ | 0.0 | mm/s | = | θ̇₁ | -0.268 | rad/s
 | -0.004 | 0.007 |  | ẏ | 40.0 | mm/s |  | θ̇₂ | 0.261 | rad/s
 | Jᵀ |  |  | End Effector Force |  |  |  | Joint Torque
 | -134.680 | -82.353 | x | Fₓ | 0.0 | N | = | τ₁ | 16470.6 | Nmm
 | -138.624 | 68.665 |  | Fy | -200.0 | N |  | τ₂ | -13733.0 | Nmm
 | (Jᵀ)⁻¹ |  |  | Joint Torque |  |  |  | End Effector Force
 | -0.003 | -0.004 | x | τ₁ | -15000 | Nmm | = | Fₓ | -9.9 | N
 | -0.007 | 0.007 |  | τ₂ | 15000 | Nmm |  | Fy | 198.4 | N

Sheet: Excluding Toe
NB: Only edit highlighted cells
End Effector Position
x | 0 | mm
y | 300 | mm
Link Dimensions
L₁ | 137.5 | mm
L₂ | 250 | mm
L₃ | 30 | mm
r | 300 | mm
φ | 1.57 | rad | 90.0 | deg
λ | 0.97 | rad | 55.8 | deg
α
θ₁ | 2.54 | rad | 145.8 | deg
θ₂ | 0.60 | rad | 34.2 | deg
Plotting
 | x | y
Origin | 0.00 | 0.00 | mm
Joint 1 | -113.68 | 77.34 | mm
Joint 2 | 113.68 | 77.34 | mm
End Effector | 0.00 | 300.00 | mm
 | Polar Coordinates
 | J |  |  | Joint Speed |  |  |  | End Effector Speed
 | 0.500 | 0.500 | x | θ̇₁ | 0.00 | rad/s | = | φ̇ | 0.0 | rad/s
 | -76.588 | 76.588 |  | θ̇₂ | 0.00 | rad/s |  | ṙ | 0.0 | mm/s
 | J⁻¹ |  |  | End Effector Speed |  |  |  | Joint Speed
 | 1.000 | -0.007 | x | φ̇ | 0.0 | rad/s | = | θ̇₁ | -261.1 | rad/s
 | 1.000 | 0.007 |  | ṙ | 40000.0 | mm/s |  | θ̇₂ | 261.1 | rad/s
 | Jᵀ |  |  | End Effector Force |  |  |  | Joint Torque
 | 0.500 | -76.588 | x | Fᵩ | 0.0 | N | = | τ₁ | -7658.8 | Nmm
 | 0.500 | 76.588 |  | Fᵣ | 100.0 | N |  | τ₂ | 7658.8 | Nmm
 | (Jᵀ)⁻¹ |  |  | Joint Torque |  |  |  | End Effector Force
 | 1.000 | 1.000 | x | τ₁ | -15000 | Nmm | = | Fᵩ | -1.818989404e-12 | N
 | -0.007 | 0.007 |  | τ₂ | 15000 | Nmm |  | Fᵣ | 195.9 | N
 | Cartesian Coordinates
 | J |  |  | Joint Speed |  |  |  | End Effector Speed
 | -150.000 | -150.000 | x | θ̇₁ | 0.00 | rad/s | = | ẋ | 0.0 | mm/s
 | -76.588 | 76.588 |  | θ̇₂ | 0.00 | rad/s |  | ẏ | 0.0 | mm/s
 | J⁻¹ |  |  | End Effector Speed |  |  |  | Joint Speed
 | -0.003 | -0.007 | x | ẋ | 0.0 | mm/s | = | θ̇₁ | -0.3 | rad/s
 | -0.003 | 0.007 |  | ẏ | 40.0 | mm/s |  | θ̇₂ | 0.3 | rad/s
 | Jᵀ |  |  | End Effector Force |  |  |  | Joint Torque
 | -150.000 | -76.588 | x | Fₓ | 0.0 | N | = | τ₁ | 15317.5 | Nmm
 | -150.000 | 76.588 |  | Fy | -200.0 | N |  | τ₂ | -15317.5 | Nmm
 | (Jᵀ)⁻¹ |  |  | Joint Torque |  |  |  | End Effector Force
 | -0.003 | -0.003 | x | τ₁ | -15000 | Nmm | = | Fₓ | 1.421085472e-14 | N
 | -0.007 | 0.007 |  | τ₂ | 15000 | Nmm |  | Fy | 195.9 | N

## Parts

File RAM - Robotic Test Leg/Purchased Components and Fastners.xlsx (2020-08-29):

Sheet: RS Components
Description | Quantity | RS Stock No. | Link | Unit Price (R) | Total (R)
24 Tooth Aluminium Timing Belt Pulley | 2 | 286-5786 | https://za.rs-online.com/web/p/timing-belt-pulleys/2865786/ | 189.17 | 378.34
Contitech 16 / T5 / 365 SS, Timing Belt, 73 Teeth, 365mm Length X 16mm Width | 2 | 474-6047 | https://za.rs-online.com/web/p/timing-belts/4746047/ | 282.29 | 564.58
Deep Groove Ball Bearing, 20mm I.D., 32mm O.D. | 2 | 619-0402 | https://za.rs-online.com/web/p/ball-bearings/6190402/ | 68.91 | 137.82
Needle Roller Bearing HK 1210, 12mm I.D., 16mm O.D. | 2 | 514-164 | https://za.rs-online.com/web/p/roller-bearings/0514164/ | 61.40 | 122.80
Deep Groove Ball Bearing, 6mm I.D., 17mm O.D. | 3 | 893-7313 | https://za.rs-online.com/web/p/ball-bearings/8937313/ | 54.57 | 163.71
RS PRO M5 x 10mm Shoulder Bolt (Box of 10) | 1 | 292-271 | https://za.rs-online.com/web/p/shoulder-bolts/0292271/ | 259.27 | 259.27
Deep Groove Ball Bearing, 10mm I.D., 19mm O.D. | 3 | 619-0064 | https://za.rs-online.com/web/p/ball-bearings/6190064/ | 42.26 | 126.78
 |  |  |  |  | 1753.30

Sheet: Fastners
Description | Size | Quantity
External Circlip | 10mm | 3
External Circlip | 20mm | 1
Hex Socket Head | M4 x 25 | 8
Hex Socket Head | M4 x 8 | 10
Hex Socket Head | M4 x 30 | 4
Hex Socket Head | M2.5 x 12 | 4
Hex Socket Countersunk Head | M4 x 12 | 8
Dowel Pin | M4 x 32 | 1
Hex Socket Head | M3 x 12 | 2
Cup Head Set Screw | M4 x 8 | 4

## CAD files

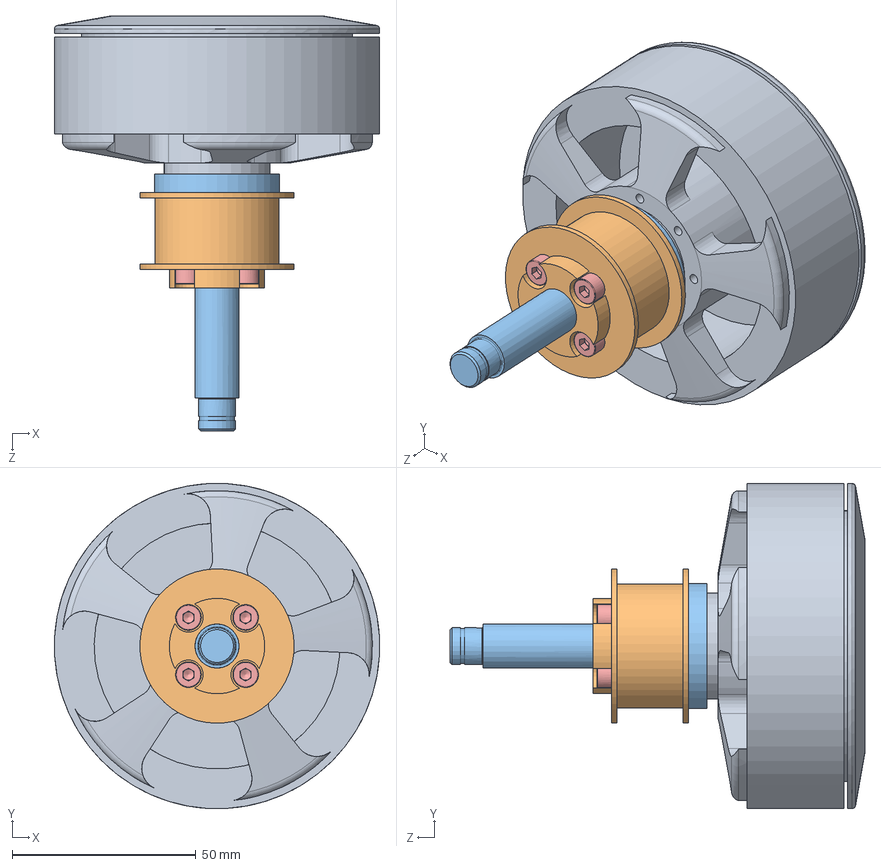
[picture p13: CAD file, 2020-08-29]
RAM - Robotic Test Leg/SolidWorks/Motor (Long) Assembly/Long Motor Assembly.sldasm
88.6 x 88.6 x 113.0 mm
T-Motor U10 KV80
Timing Belt Pulley
Motor Shaft Long
ISO 10642 - M4 x 12 - 12C x 4
ISO 4762 M4 x 25 - 25C x 4

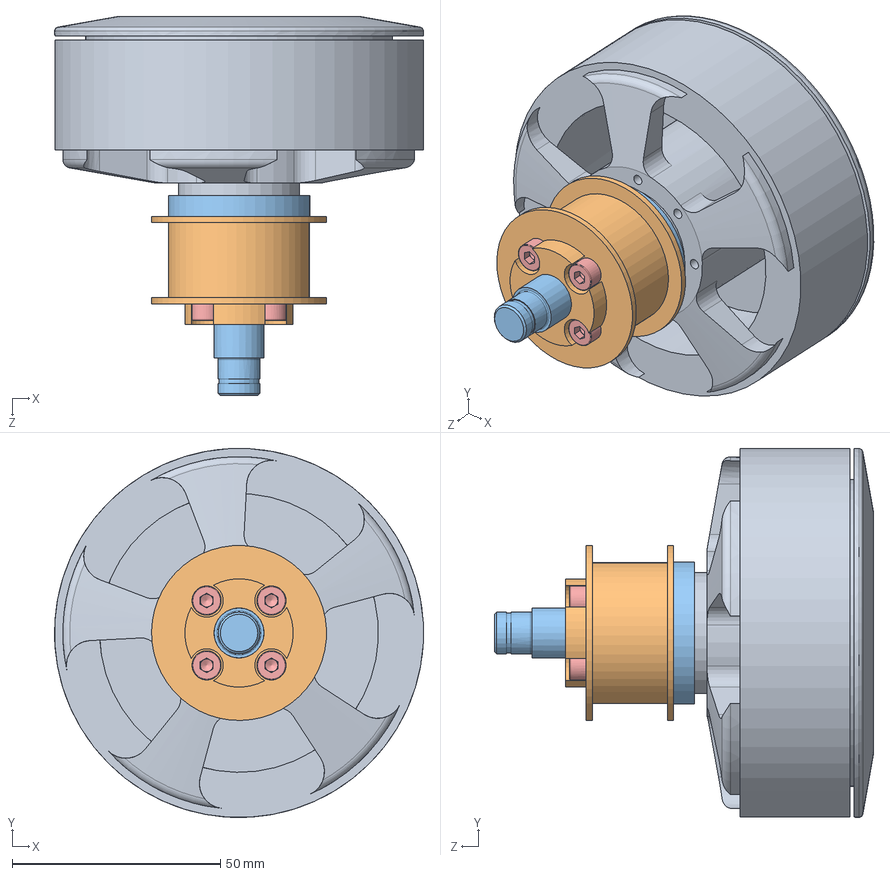
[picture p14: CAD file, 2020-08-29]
hopper-boom-attachment/hopper-model/Motor (Short) Assembly/Short Motor Assembly.sldasm
88.6 x 88.6 x 91.0 mm
T-Motor U10 KV80
Timing Belt Pulley
Motor Shaft Short
ISO 10642 - M4 x 12 - 12C x 4
ISO 4762 M4 x 25 - 25C x 4

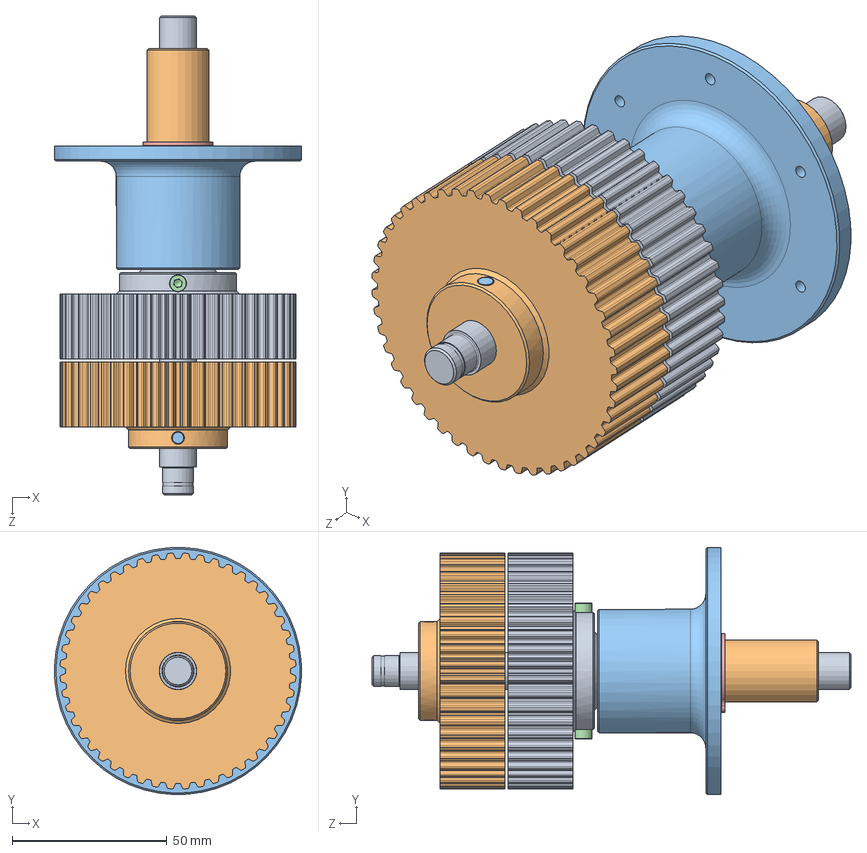
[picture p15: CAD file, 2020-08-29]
RAM - Robotic Test Leg/SolidWorks/Coaxial Shaft Assembly/Coaxial Shaft Assembly.sldasm
79.9 x 79.9 x 155.0 mm
Inner Shaft
Outer Shaft
Flange
SKF - 61804 - 18,SI,NC,18_68 x 2
Circlip DIN 471 - 20 x 1.2
_HK_1210_PART1_2 x 2
_HK_1210_PART2_4 x 36
_HK_1210_PART3_23 x 36
Outer Timing Belt Gear
Inner Timing Belt Gear
ISO 8734 - 4 x 32 - A - St
ISO 4762 M3 x 12 - 12C x 2

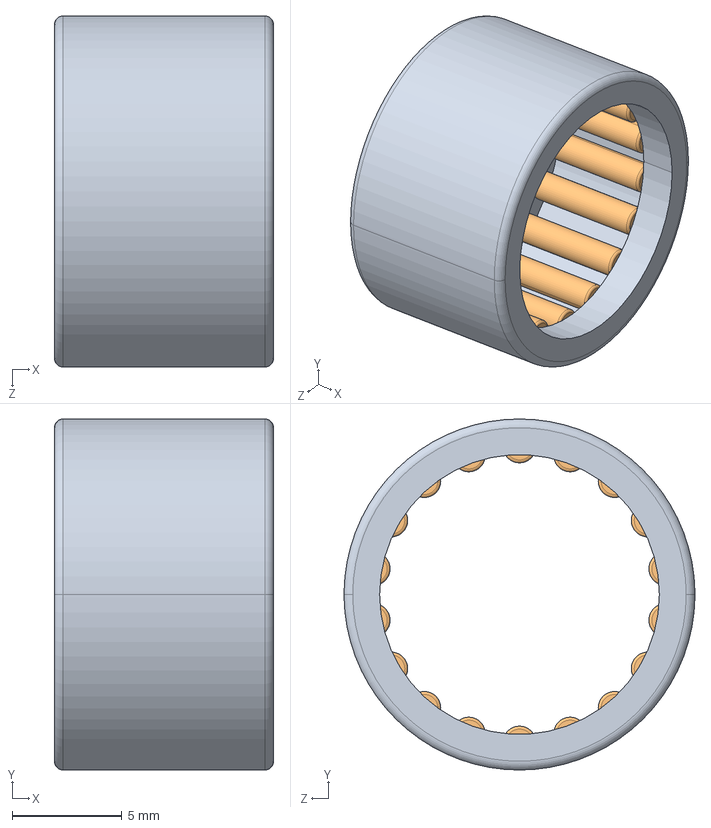
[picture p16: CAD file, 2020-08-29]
hopper-boom-attachment/hopper-model/Coaxial Shaft Assembly/HK_1210.sldasm
10.0 x 16.0 x 16.0 mm
_HK_1210_PART1_2
_HK_1210_PART2_4 x 18
_HK_1210_PART3_23 x 18

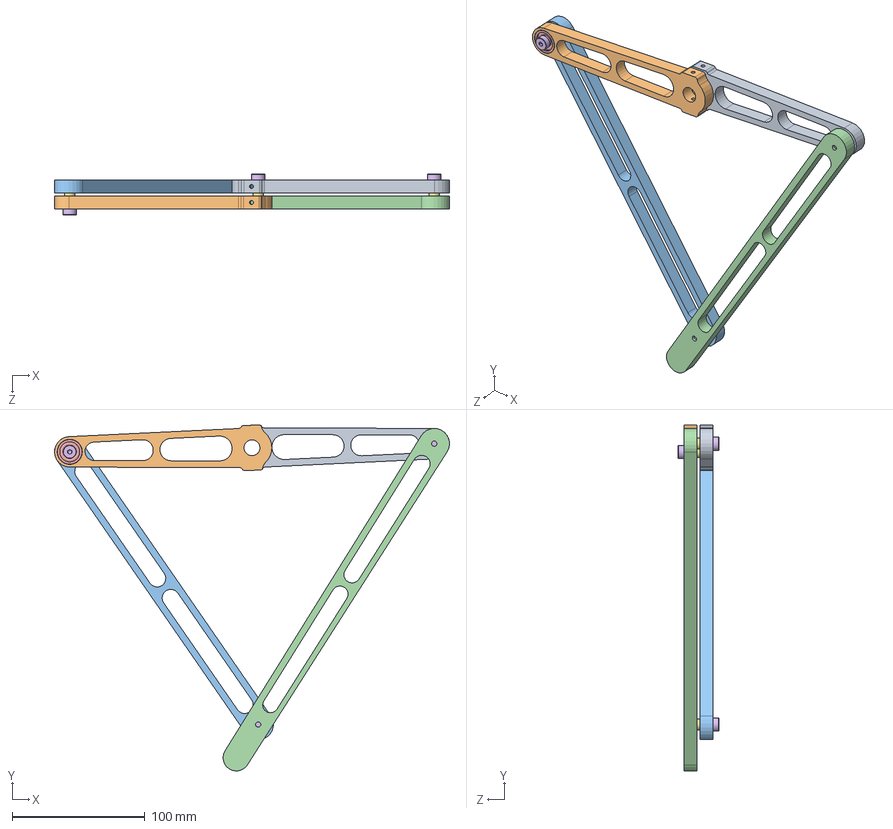
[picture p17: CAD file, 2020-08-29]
hopper-boom-attachment/hopper-model/Leg Assembly/Leg Assembly.SLDASM
297.9 x 260.9 x 31.0 mm
Outer Short Link
Inner Short Link
Long Link
Extra Long Link
SKF - 626 - 8,SI,NC,8_68 x 3
ISO 7379 - 6 x 10 --- C x 3
Leg Spacer x 3

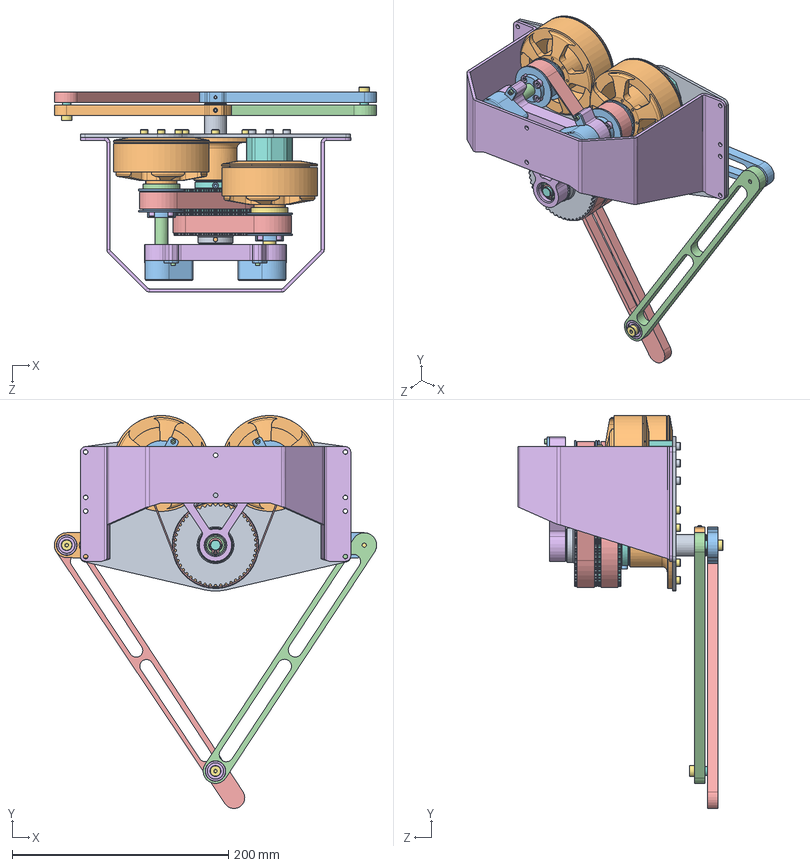
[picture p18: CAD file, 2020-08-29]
hopper-boom-attachment/hopper-model/Assembly.SLDASM
298.0 x 363.3 x 189.5 mm
Mounting Plate
T-Motor U10 KV80 x 2
Timing Belt Pulley x 2
Motor Shaft Long
ISO 10642 - M4 x 12 - 12C x 8
ISO 4762 M4 x 25 - 25C x 8
Motor Shaft Short
Inner Shaft
Outer Shaft
Flange
SKF - 61804 - 18,SI,NC,18_68 x 2
Circlip DIN 471 - 20 x 1.2
_HK_1210_PART1_2 x 2
_HK_1210_PART2_4 x 36
_HK_1210_PART3_23 x 36
Outer Timing Belt Gear
Inner Timing Belt Gear
ISO 8734 - 4 x 32 - A - St
ISO 4762 M3 x 12 - 12C x 2
SKF - 61800 - 14,SI,NC,14_68 x 3
Circlip DIN 471 - 10 x 1 x 3
Support Brace
ISO 4762 M4 x 8 - 8C x 10
Motor Mounting
ISO 4762 M4 x 30 - 20C x 4
Outer Short Link
Inner Short Link
Long Link
Extra Long Link
SKF - 626 - 8,SI,NC,8_68 x 3
ISO 7379 - 6 x 10 --- C x 3
Leg Spacer x 3
ISO 4029 - M4 x 8-C x 4
Encoder Shaft x 2
HEDL-5640-A13 Encoder x 2
ISO 4762 M2.5 x 12 - 12C x 4
Contitech T5 365mm Timing Belt x 2
hopper-boom-attachment

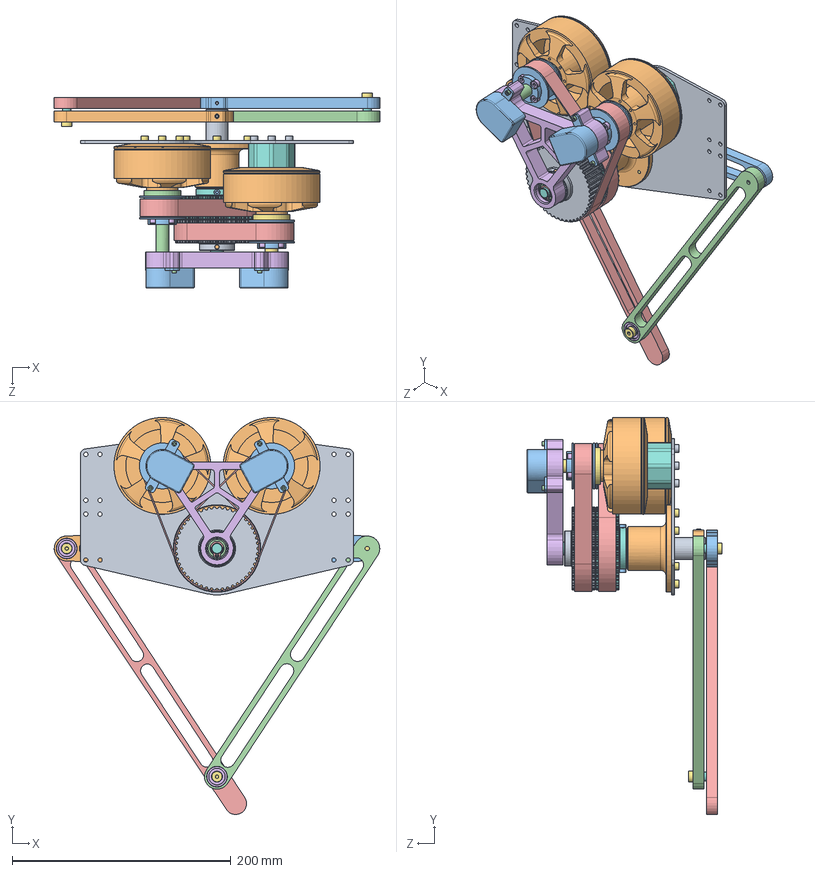
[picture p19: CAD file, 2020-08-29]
RAM - Robotic Test Leg/SolidWorks/Assembly.SLDASM
298.0 x 363.3 x 178.8 mm
Mounting Plate
T-Motor U10 KV80 x 2
Timing Belt Pulley x 2
Motor Shaft Long
ISO 10642 - M4 x 12 - 12C x 8
ISO 4762 M4 x 25 - 25C x 8
Motor Shaft Short
Inner Shaft
Outer Shaft
Flange
SKF - 61804 - 18,SI,NC,18_68 x 2
Circlip DIN 471 - 20 x 1.2
_HK_1210_PART1_2 x 2
_HK_1210_PART2_4 x 36
_HK_1210_PART3_23 x 36
Outer Timing Belt Gear
Inner Timing Belt Gear
ISO 8734 - 4 x 32 - A - St
ISO 4762 M3 x 12 - 12C x 2
SKF - 61800 - 14,SI,NC,14_68 x 3
Circlip DIN 471 - 10 x 1 x 3
Support Brace
ISO 4762 M4 x 8 - 8C x 10
Motor Mounting
ISO 4762 M4 x 30 - 20C x 4
Outer Short Link
Inner Short Link
Long Link
Extra Long Link
SKF - 626 - 8,SI,NC,8_68 x 3
ISO 7379 - 6 x 10 --- C x 3
Leg Spacer x 3
ISO 4029 - M4 x 8-C x 4
Encoder Shaft x 2
HEDL-5640-A13 Encoder x 2
ISO 4762 M2.5 x 12 - 12C x 4
Contitech T5 365mm Timing Belt x 2

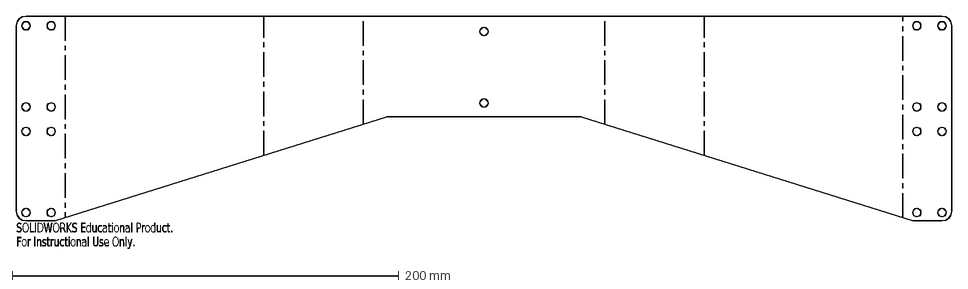
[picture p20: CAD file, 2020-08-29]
hopper-boom-attachment/Flat-Pattern - hopper-boom-attachment.DXF
SOLIDWORKS Educational Product.
For Instructional Use Only.

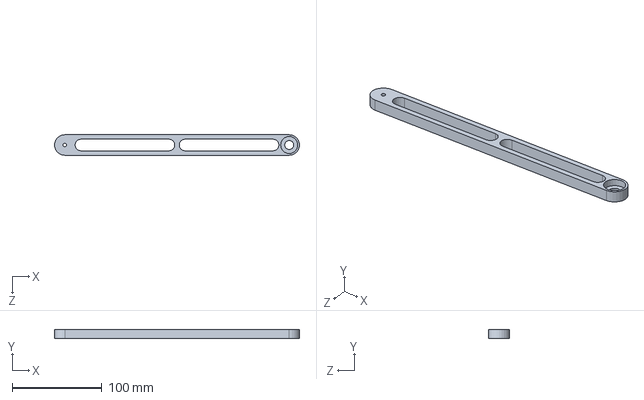
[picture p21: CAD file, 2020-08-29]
hopper-boom-attachment/hopper-model/Leg Assembly/Long Link.SLDPRT
273.0 x 10.0 x 23.0 mm

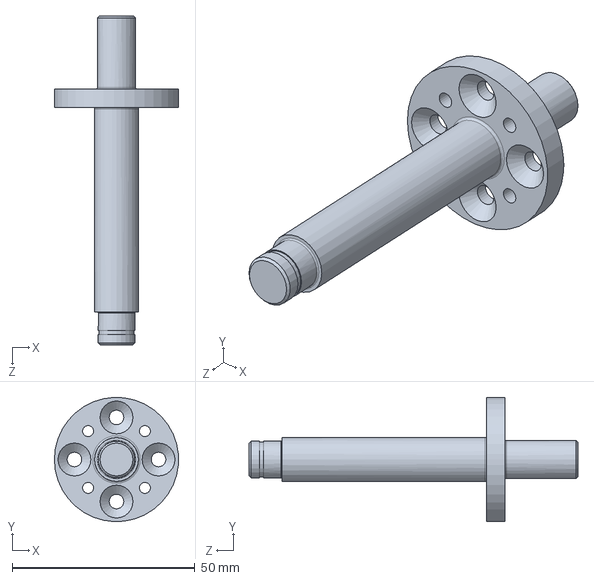
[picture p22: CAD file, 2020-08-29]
hopper-boom-attachment/hopper-model/Motor (Long) Assembly/Motor Shaft Long.SLDPRT
34.0 x 34.0 x 90.0 mm

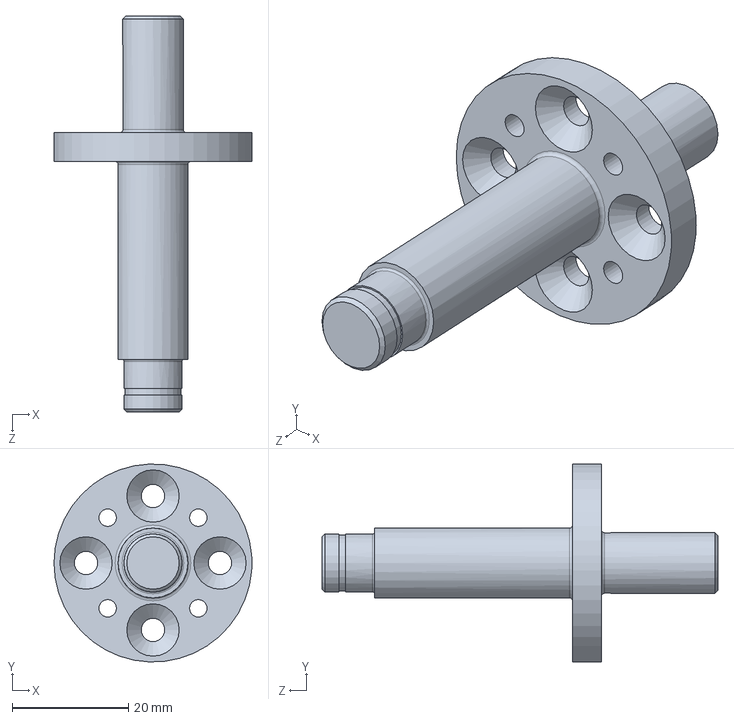
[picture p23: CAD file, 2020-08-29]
hopper-boom-attachment/hopper-model/Motor (Short) Assembly/Motor Shaft Short.SLDPRT
34.0 x 34.0 x 68.0 mm

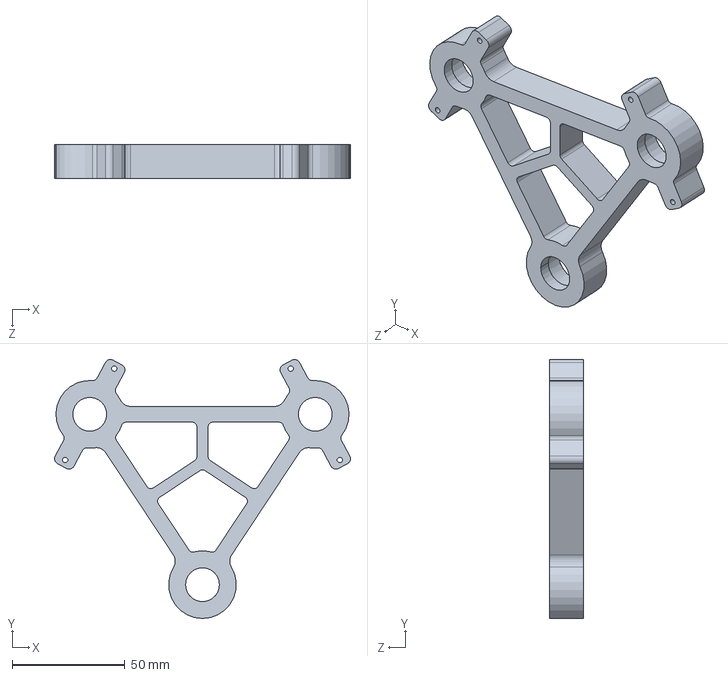
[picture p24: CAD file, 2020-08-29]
hopper-boom-attachment/hopper-model/Support Brace.SLDPRT
131.3 x 114.9 x 15.0 mm

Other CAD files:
hopper-boom-attachment/hopper-model/Motor (Long) Assembly/Long Motor Assembly.sldasm
RAM - Robotic Test Leg/SolidWorks/Motor (Short) Assembly/Short Motor Assembly.sldasm
hopper-boom-attachment/hopper-model/Coaxial Shaft Assembly/Coaxial Shaft Assembly.sldasm
RAM - Robotic Test Leg/SolidWorks/Leg Assembly/Leg Assembly.SLDASM
hopper-boom-attachment/hopper-model/Coaxial Shaft Assembly/_HK_1210_PART1_2.sldprt
RAM - Robotic Test Leg/3D Printing STL Files/Encoder Shaft.STL
RAM - Robotic Test Leg/3D Printing STL Files/Leg Spacer.STL
RAM - Robotic Test Leg/3D Printing STL Files/Motor Mounting.STL
RAM - Robotic Test Leg/3D Printing STL Files/Support Brace.STL
RAM - Robotic Test Leg/Laser Cutting DXF Files/Leg_Links - 10mm 5182 Aluminium.DXF
RAM - Robotic Test Leg/Laser Cutting DXF Files/Mounting_Plate - 3mm 5182 Aluminium.DXF
RAM - Robotic Test Leg/SolidWorks/Coaxial Shaft Assembly/Flange.SLDPRT
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

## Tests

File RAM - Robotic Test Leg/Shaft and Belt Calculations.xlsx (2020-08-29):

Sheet: Inner Shaft
NB: Only edit highlighted cells
Yield Strength | 215 | MPa | 304 Stainless Steel
Bending Moment (M) | 16.61 | Nm
Torque (T) | 15 | Nm
Diameter | 0.012 | m
Sigma | 97.91 | MPa
Tau | 44.21 | MPa
RF | 1.73

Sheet: Outer Shaft
NB: Only edit highlighted cells
Yield Strength | 215 | MPa | 304 Stainless Steel
Bending Moment (M) | 30.73 | Nm
Torque (T) | 15 | Nm
Outer Diameter | 0.02 | m
Inner Diameter | 0.016 | m
Sigma | 66.27 | MPa
Tau | 16.17 | MPa
RF | 2.99

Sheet: Belt
NB: Only edit highlighted cells
Pitch | 5 | mm
Centre Distance | 90.48 | mm
 | Gear 1 | Gear 2
No. Teeth | 24 | 48 | teeth
Pitch Diameter | 38.20 | 76.39 | mm
Angle of Wrap | 2.72 | 3.57 | rad
Belt Length | 365.00 | mm

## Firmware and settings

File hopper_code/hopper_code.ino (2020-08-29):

// constants *************************************************
// left and right motors
// these aren't pins, just the motor numbers
const int motor_0 = 0;
const int motor_1 = 1;

// Encoder Counts Per Revolution (CPR) = 4x Pulse Per Revolution (PPR)
const unsigned int ENCODER_CPR = 4096;
inline float rad2motorpos(float angle) {
  return angle/3.14f * 4096.0f;
}

// waypoints (in radians) that the motors should follow
// these vectors should all be the same length
// at timestep[i] (measured in milliseconds), motor_0 should be
// at waypts_0[i] rads
//const float waypts_0[] =        {  0.5,  1.0,  0.0, -0.5,  0.0, 3.14 };
const float waypts_0[] =        {  0.0,  0.5,  0.0, -0.5,  0.0,  0.5 };
const float waypts_1[] =        {  0.0,  0.0,  0.5, -0.5,  0.0,  0.5 };
const unsigned long timepts[] = { 1000, 2000, 3000, 4000, 5000, 6000 };
const unsigned int num_waypts = 6;



// pins *****************************************************
// https://docs.odriverobotics.com/interfaces#uart
const uint8_t ODRIVE_RX = 0; // odrive GPIO 1 = Tx
const uint8_t ODRIVE_TX = 1; // odrive GPIO 2 = Rx

const uint8_t ENCODER_YAW_A = 9;
const uint8_t ENCODER_YAW_B = 10;
const uint8_t ENCODER_PITCH_A = 11;
const uint8_t ENCODER_PITCH_B = 12;

const uint8_t STOP_BUTTON = 3;
volatile bool should_stop = false;
void emergency_stop() { should_stop = true; }



// ODrive ****************************************************
#include <SoftwareSerial.h>  // TODO: why am I using this instead of Serial?
#include <ODriveArduino.h>

// RX (ODrive TX), TX (ODrive RX)
SoftwareSerial odrive_serial(ODRIVE_RX, ODRIVE_TX);
ODriveArduino odrive(odrive_serial);


// Encoder ****************************************************
// https://www.pjrc.com/teensy/td_libs_Encoder.html
#include <Encoder.h>
Encoder global_yaw(ENCODER_YAW_A, ENCODER_YAW_B);
Encoder global_pitch(ENCODER_PITCH_A, ENCODER_PITCH_B);


// vs code arduino complains about not knowing what serial is otherwise
#ifdef USBCON
#define Serial Serial1
#endif

// setup ******************************************************
void setup() {
  // Serial to PC
  Serial.begin(115200);
  while (!Serial.availableForWrite()) ;  // wait for Serial Monitor to open

  pinMode(STOP_BUTTON, INPUT_PULLUP);
  attachInterrupt(digitalPinToInterrupt(STOP_BUTTON), emergency_stop, LOW);
  
  odrive_serial.begin(115200);
  // Serial << "axis0: requesting encoder index search...";
  // run_state(motor_0, ODriveArduino::AXIS_STATE_ENCODER_INDEX_SEARCH);
  // Serial << "axis1: requesting encoder index search...";
  // run_state(motor_1, ODriveArduino::AXIS_STATE_ENCODER_INDEX_SEARCH);
  // delay(1000);

  // odrv0.axis0.controller.config.control_mode = CTRL_MODE_POSITION_CONTROL??
  Serial << "Setting motors to closed loop control" << '\n';
  odrive.run_state(motor_0, ODriveArduino::AXIS_STATE_CLOSED_LOOP_CONTROL, false);
  odrive.run_state(motor_1, ODriveArduino::AXIS_STATE_CLOSED_LOOP_CONTROL, false);

  Serial << "BEGIN LOGGING" << '\n';
  Serial << "global_yaw,global_pitch" << '\n';

  // TODO: replace delay with waiting for a button event or something?
  delay(0.5);

  odrive.SetPosition(motor_0, rad2motorpos(waypts_0[0]), 1024.0f);
  odrive.SetPosition(motor_1, rad2motorpos(waypts_1[0]), 1024.0f);
}

// loop ********************************************************
void loop() {
  static unsigned int ptr = 0;             // pointer into waypts
  static unsigned long t_start = millis(); // time since first loop
  unsigned long t_loop_start = millis();   // time since loop started
  
  // read encoders and log to serial
  //Serial << global_yaw.read()/4096.0f << ',' << global_pitch.read()/4096.0f << '\n';

  // read esimated motor positions
  odrive_serial << "r axis0.encoder.pos_estimate\n";
  Serial << odrive.readFloat();
  odrive_serial << "r axis1.encoder.pos_estimate\n";
  Serial << ',' << odrive.readFloat() << '\n';
  
  // inc array pointer if past time
  if (millis() > timepts[ptr] + t_start) {
    if (ptr + 1 >= num_waypts) {
      should_stop = true;
    } else {
      ptr += 1;

      // calculate correct angle
      // ...........
      // ...........
  
      // set next position
      odrive.SetPosition(motor_0, rad2motorpos(waypts_0[ptr]), 1024.0f);
      odrive.SetPosition(motor_1, rad2motorpos(waypts_1[ptr]), 1024.0f);
    }
  }

  if (should_stop) {
    Serial << "END LOGGING" << '\n';
    Serial << "Setting motors to idle" << '\n';
    odrive.run_state(motor_0, ODriveArduino::AXIS_STATE_IDLE, false);
    odrive.run_state(motor_1, ODriveArduino::AXIS_STATE_IDLE, false);
    for (;;) {};
  }

  // 50 Hz control loop - wait for correct time
  unsigned int loop_time = millis() - t_loop_start;
  if (loop_time < 50) {
    delay(50 - loop_time);
  }
}


// other functions *******************************************
void setup_motor(int motornum) {
  //Serial << "axis" << motornum << ": requesting full calibration sequence...";
  //_run_state(motornum, ODriveArduino::AXIS_STATE_FULL_CALIBRATION_SEQUENCE);

  // Serial << "axis" << motornum << ": requesting encoder offset calibration...";
  // _run_state(motornum, ODriveArduino::AXIS_STATE_ENCODER_OFFSET_CALIBRATION);

  // Serial << "axis" << motornum << ": requesting motor calibration...";
  // _run_state(motornum, ODriveArduino::AXIS_STATE_MOTOR_CALIBRATION);

  Serial << "axis" << motornum << ": requesting encoder index search...";
  run_state(motornum, ODriveArduino::AXIS_STATE_ENCODER_INDEX_SEARCH);
  
  Serial << "axis" << motornum << ": requesting closed loop control...";
  run_state(motornum, ODriveArduino::AXIS_STATE_CLOSED_LOOP_CONTROL);
}

void run_state(int motornum, int requested_state) {
  int success = odrive.run_state(motornum, requested_state, true);
  if (success) {
    Serial << " success :)" << '\n';
  } else {
    Serial << " failed :(" << '\n';
  }
}

// printing with stream operator
template<class T> inline Print& operator <<(Print &obj,     T arg) {
  obj.print(arg);    return obj;
}
template<>        inline Print& operator <<(Print &obj, float arg) {
  obj.print(arg, 4); return obj;
}

// attic ******************************************************
/*
odrive_serial << "r axis" << motor_0 << ".encoder.config.cpr\n";
Serial << "debug: " << odrive.readInt() << '\n';
*/
/*
  Serial << "Setting to position " << rad2motorpos(waypts_0[ptr])
          << " via ptr = " << ptr
          << " and angle = " << waypts_0[ptr] << "rad" << '\n';
*/

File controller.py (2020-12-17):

"""
This script is NOT meant to be running via the command
line. Instead, activate the conda environment, launch
ipython:

    $ ipython

and then copy-paste in commands block by block. When
you feel that a certain block of code is working well,
copy it into the `lib.py` file

By default, if you update the `lib.py` file, the changes
won't reflect in a live IPython session. Change that by
copying in the following code:

    >>> %load_ext autoreload
    >>> %autoreload 2

See eg. https://alknemeyer.github.io/jupyter-notebook-workflow/#autoreloading-changed-code
"""

########################################## SET UP
import time
from scripts import lib
from scripts.lib import (
    PositionControl, set_foot_position as setfoot,
)
import odrive
odrv0 = odrive.find_any()

# move leg straight down (so the foot is below the axle,
# as far down as possible) then run the line of code below
# Doing so gets everything to a "known start position"
# Simple using the index lines of the encoders would be
# better, though!
lib.zero_motors_no_index_straightdown(odrv0)
odrv0

########################################## SIMPLE TESTS
from scripts import test
test.increment(odrv0, delta=100)  # + = bend knees
test.slipping(odrv0)
test.slow_position_control(odrv0)

########################################## INCREASE CURRENT LIMITS
odrv0.axis0.motor.config.current_lim = 20
odrv0.axis1.motor.config.current_lim = 20

odrv0.axis0.motor.config.current_lim_tolerance = 4
odrv0.axis1.motor.config.current_lim_tolerance = 4


########################################## SIMPLE LAUNCH
with PositionControl(odrv0):
    # lib.fast_gains(odrv0)
    lib.set_gains(odrv0, pos_scale=3, vel_scale=5, bandwidth_hz=10)
    th0, th1 = lib.foot_xy_to_th_deg(x_m=0, y_m=-0.35)
    lib.set_to_nearest_angle(odrv0, th0, motornum=0)#, vel_limit=180)
    lib.set_to_nearest_angle(odrv0, th1, motornum=1)#, vel_limit=180)
    time.sleep(2)

    lib.slow_gains(odrv0)
    th0, th1 = lib.foot_xy_to_th_deg(x_m=0, y_m=-0.15)
    lib.set_to_nearest_angle(odrv0, th0, motornum=0, vel_limit=180)
    lib.set_to_nearest_angle(odrv0, th1, motornum=1, vel_limit=180)
    time.sleep(2)


########################################## LOG REPEATED JUMPS
"""
You might need to adjust the permissions for any plugged in
sensors/the teensy. On Ubuntu, this will be something like:

    $ sudo chmod 666 /dev/ttyACM1

Or from the Python session:

    >>> import os
    >>> os.system('sudo chmod 666 /dev/ttyACM0')

Log the optoforce at the same time, in another terminal:

    $ python scripts/optoforce.py
    $ python scripts/plot_optoforce.py

BUT Alex suggests rather incorporating it into the
`log_while_delaying()` function, which would make the
data accessible to the control and make absolutely sure
that the readings are all synced up
"""
import csv
from datetime import datetime

# this requires the sensor-logger submodule to be downloaded
# and named as sensor_logger
from sensor_logger.scripts import receive_comms

# might need to adjust the port
# run this once only, since reconnecting could cause issues!
logger = receive_comms.TeensyLogger(port='/dev/ttyACM3')

# check that it reads without issue. We don't want the line
# to just hang in the control loop
logger.read()

data = []
experiment_start_datetime = datetime.now().strftime("%H-%M-%S")


def log_while_delaying(delay: float):
    tstart = time.time()
    while time.time() < tstart + delay:
        data.append([*logger.read(), *lib.upper_leg_angles_deg(odrv0)])


# go into crouch position, then launch, then try to land
with PositionControl(odrv0):
    while True:
        try:
            # crouch
            setfoot(odrv0, x_m=0, y_m=-0.15, gains='medium', vel_limit=360)
            log_while_delaying(2.)

            # launch
            lib.set_gains(odrv0, pos_scale=5, vel_scale=5, bandwidth_hz=10)
            setfoot(odrv0, x_m=0, y_m=-0.38)#, vel_limit=360)
            log_while_delaying(0.4)

            # impact
            setfoot(odrv0, x_m=0, y_m=-0.2, gains='medium', vel_limit=360)
            log_while_delaying(2.)

        except KeyboardInterrupt:
            break


with open(f'data/leg-data-{experiment_start_datetime}.csv', 'w', newline='') as csvfile:
    writer = csv.writer(csvfile)
    header = receive_comms.PACKET_HEADER + ['th_ul [deg]', 'th_ur [deg]', 'dth_ul [deg/s]', 'dth_ur [deg/s]']
    writer.writerow(header)
    writer.writerows(data)


########################################## ATTIC


# from optoforce import OptoForce16 as OptoForce
# def read_foot_forces_2D(force_sensor: OptoForce):
#     reading = force_sensor.read(only_latest_data=True)
#     return {'L_x': reading.Fy, 'L_y': reading.Fz}

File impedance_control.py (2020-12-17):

"""
For general documentation, rather read through `controller.py`
first
"""
from scripts import lib
from scripts.lib import CurrentControl
import odrive
odrv0 = odrive.find_any()


########################################## INCREASE CURRENT
## you MIGHT want to increase the current available
## to each motor:
# for ax in (odrv0.axis0, odrv0.axis1):
#     ax.motor.config.current_lim = 15
#     ax.motor.config.current_lim_tolerance = 3


########################################## MOTOR ANGLE IMPEDANCE CONTROL
kp = 0.2
kd = kp/10
th_ul, th_ur, dth_ul, dth_ur = lib.upper_leg_angles_deg(odrv0)
controller0 = lib.PDControl(th_ur, 0, kp, kd)  # -40 to launch
controller1 = lib.PDControl(th_ul, 0, kp, kd)  # +40 to launch

with CurrentControl(odrv0):
    while True:
        try:
            th_ul, th_ur, dth_ul, dth_ur = lib.upper_leg_angles_deg(odrv0)
            curr0 = controller0(th_ur, dth_ur)
            curr1 = controller1(th_ul, dth_ul)
            lib.set_current(odrv0, motor0=curr0, motor1=curr1)
        except KeyboardInterrupt:
            break


########################################## LEG POSITION IMPEDANCE CONTROL
# TODO: what is 0 deg? SHOULD be pointing right!
#       also: radians vs degrees?
#       also: positive vs negative angles/current??
from scripts import controller_generated as cg

th_ul, th_ur, dth_ul, dth_ur = lib.upper_leg_angles(odrv0)  # radians

r, th, dr, dth = cg.foot_state_polar(th_ul, th_ur, dth_ul, dth_ur, lib.l3x, lib.l3y)

ddr_controller = lib.PDControl(r, dr, kp=0.01, kd=0.001)
ddth_controller = lib.PDControl(th, dth, kp=0.01, kd=0.001)

with CurrentControl(odrv0):
    while True:
        try:
            th_ul, th_ur, dth_ul, dth_ur = lib.upper_leg_angles(odrv0)  # rads
            r, th, dr, dth = cg.foot_state_polar(th_ul, th_ur, dth_ul, dth_ur, lib.l3x, lib.l3y)
            if th_ul == th_ur:  # getting weird errors if the angles are the same?
                th_ul += 0.001
            try:
                curr0, curr1 = cg.impedance_control(
                    ddr_setpoint=ddr_controller(r, dr),
                    ddth_setpoint=ddth_controller(th, dth),
                    th_ul=th_ul, th_ur=th_ur, dth_ul=dth_ul, dth_ur=dth_ur,
                    L_x=0, L_y=0, l3x=lib.l3x, l3y=lib.l3y, Kt=lib.torque_constant,
                )
                lib.set_current(odrv0, motor0=-5*curr0, motor1=0)
                print('current:', curr0, curr1)
            except ZeroDivisionError:
                print('error!')
        except KeyboardInterrupt:
            break

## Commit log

2020-09-11 Update arduino/C++ paths
2020-09-11 Mention need to clone ODrive git repo
2020-09-11 Document wiring configuration
2020-09-11 Remove encoder code, move to controller/ folder
2020-09-18 Make folder for data
    [foot-trajectory-data.xlsx]
2020-09-18 Don't track attic.py
2020-09-18 Add WIP script for leg control
2020-09-28 track attic
2020-09-30 Add foot force/torque mapping stuff
2020-09-30 Simple type stubs for odrive (IDE completion)
2020-10-06 Add code to test encoders
2020-10-06 Mention odrive firmware version
2020-10-07 Reboot before config to not accidentally save nonsense
    [config_motors.py]
2020-10-22 Need to rerun config; install odrive package
2020-10-22 Document; lower current lim; clear errors on dump
    [config_motors.py]
2020-10-24 Move odrive type stubs to separate repo
2020-10-24 remove ODrive repo, add movie stuff
2020-10-30 Add arduino height sensor code
2020-11-03 Test script to read from teensy
2020-11-04 Refactor index zeroing, be explicit about current lims
2020-11-04 Add masses, current control
2020-11-13 Remove print statements
2020-11-13 Add script to find torque constant
2020-11-13 Add torque constant test
2020-11-13 Refactor arduino code
2020-11-17 Remove generated function, rename encoder set func
2020-11-18 Updated typing for odrive.find_any()
2020-11-19 Add printing and plot at end
2020-11-19 Increasing calibration current; don't search for index at startup
2020-12-09 Initial code for teensy logger - untested!
2020-12-09 Don't track logged data
2020-12-09 Add diagram of leg
2020-12-09 Fix degrees/radians bug, start on foot offsets
    [controller.py, lib.py]
2020-12-10 Receive imu data
2020-12-11 Teensy logger code + laptop reciever = working
2020-12-15 Move sensor logger code to its own repo
2020-12-15 Fix encoder issue
2020-12-15 Make max leg length a variable; add missing args
    [lib.py, test.py]
2020-12-15 Rename sensor logger to something importable (ugh)
2020-12-15 "sensor-logger" added as "sensor_logger"
2020-12-17 Add some sample data, delete the rest
    [foot-trajectory-data.xlsx, leg-data-001.csv]
